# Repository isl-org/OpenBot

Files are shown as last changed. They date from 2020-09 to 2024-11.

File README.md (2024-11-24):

<a href="https://www.openbot.org/" target="_blank">
  Banner
</a>

<h1 align="center"><a>Turning Smartphones into Robots</a></h1>

<p align="center">
   </a>
   </a>
   </a>
   </a>
   </a>
   </a>
   </a>
   </a>
</p>

<p align="center">
  <span>English</span> |
  <a href="README.zh-CN.md">简体中文</a> |
  <a href="README.de-DE.md">Deutsch</a> |
  <a href="README.fr-FR.md">Français</a> |
  <a href="README.es-ES.md">Español</a> |
  <a href="README.ko-KR.md">한국어</a>
</p>

OpenBot leverages smartphones as brains for low-cost robots. We have designed a small electric vehicle that costs about $50 and serves as a robot body. Our software stack for Android smartphones supports advanced robotics workloads such as person following and real-time autonomous navigation.

## Get started with OpenBot

- Read the [Disclaimer](DISCLAIMER.md)
- Build your own [Robot Body](body/README.md)
- Flash the [Arduino Firmware](firmware/README.md)
- Install the [Android Apps](android/README.md)
- Drive the robot via a [Controller](controller/README.md)
- Program your robot in the [Playground](open-code/README.md)
- Train your own [Driving Policy](policy/README.md)

## Get the source code

- You can download the repo as a [zip file](https://github.com/intel-isl/OpenBot/archive/master.zip) and extract it into a folder of your choice.
- You can clone the OpenBot repository from GitHub with the following command:
    ```bash
    git clone https://github.com/intel-isl/OpenBot.git
    ```
- You can fork the OpenBot repository and then clone your local copy. This is recommended, especially if you want to [contribute](CONTRIBUTING.md).

## Videos

<a href="https://www.youtube.com/watch?v=RbzPXywJifA" >
  youtube video
</a>

<a href="https://www.youtube.com/watch?v=qc8hFLyWDOM" >
  youtube video
</a>

## Cool projects using OpenBot

There are a lot of cool projects using OpenBot already. Below is a small selection. Click on the images to be redirected to the respective projects.

<p float="left">
  <a href="https://www.thingiverse.com/thing:4670884" target="_blank">
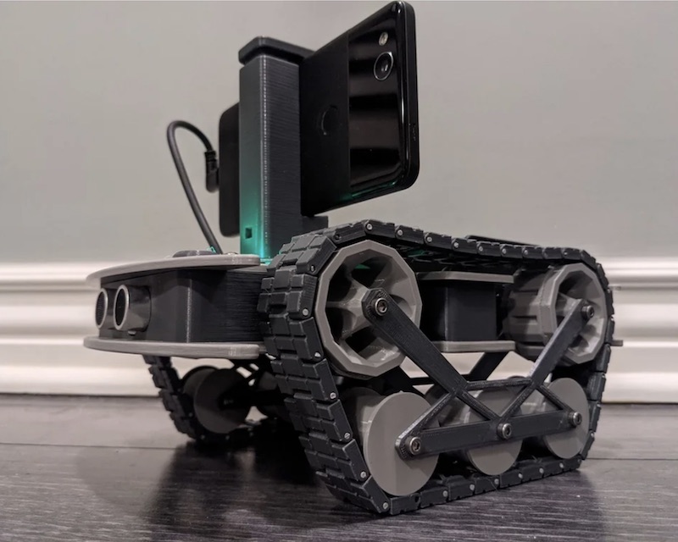
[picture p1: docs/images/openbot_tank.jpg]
Tank OpenBot
    
  </a>
  <a href="https://diyrobocars.com/2020/12/14/an-improved-version-of-the-intel-openbot" target="_blank">
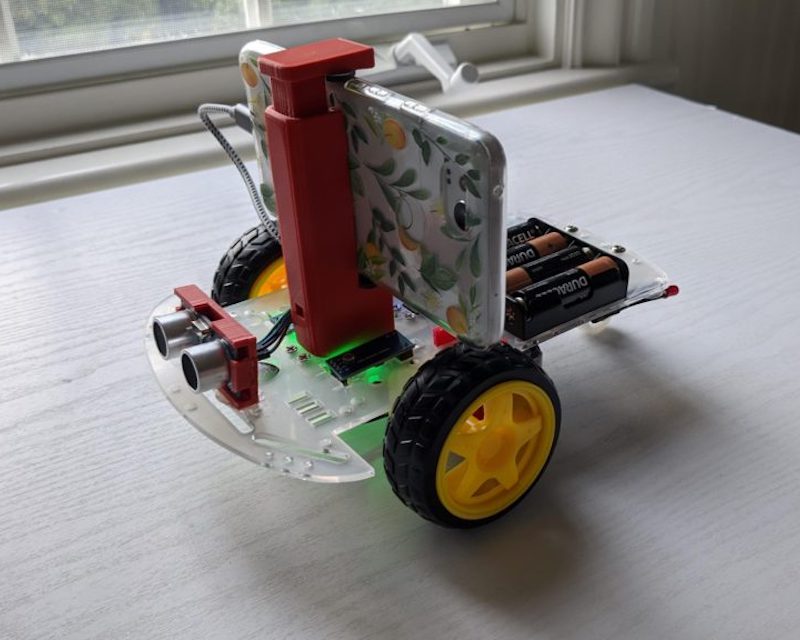
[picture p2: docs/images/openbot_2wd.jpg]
2WD OpenBot
    
  </a>
  <a href="https://custom-build-robots.com/raspberry-pi-robot-cars/openbot-your-smartphone-controls-a-robot-car-introduction/13860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" target="_blank">
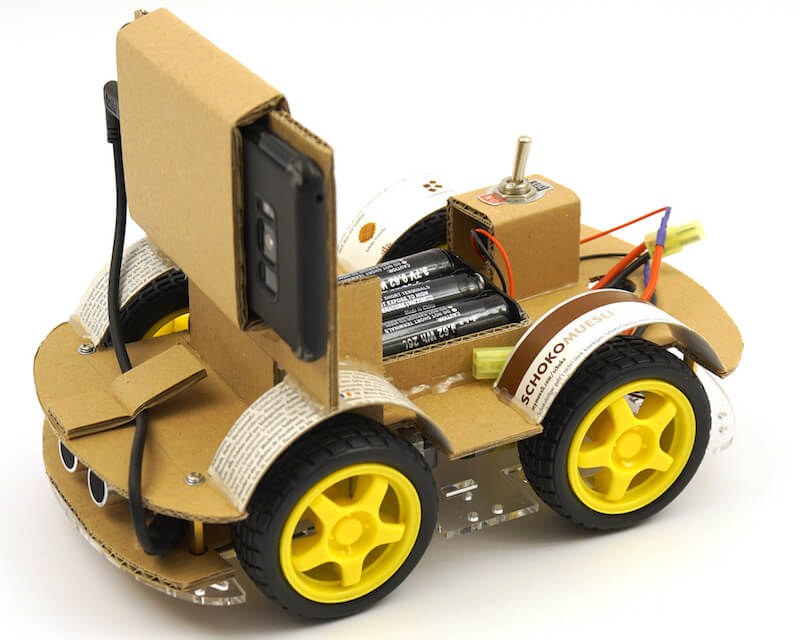
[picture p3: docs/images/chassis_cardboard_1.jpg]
Cardboard OpenBot
    
  </a>
  <a href="https://www.youtube.com/watch?v=PEj8jWapGt4" target="_blank">
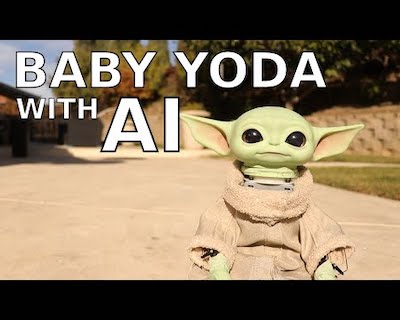
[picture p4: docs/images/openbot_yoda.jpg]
Baby Yoda OpenBot
    
  </a>
</p>

## Contact

- Join our [Slack](https://join.slack.com/t/openbot-community/shared_invite/zt-jl8ygxqt-WNRNi9yzh7Lu60qui6Nh6w) channel to connect with the OpenBot community.
- Contact us via [Email](mailto:openbot.team@gmail.com)

## Contribute

Please read the [contribution guidelines](CONTRIBUTING.md). If you are not sure where to start have a look at the [open issues](https://github.com/intel-isl/OpenBot/issues).

## Citation

Please cite our [paper](https://arxiv.org/abs/2008.10631) if you use OpenBot.

```bib
@inproceedings{mueller2021openbot,
    title     = {OpenBot: Turning Smartphones into Robots},
    author    = {M{\"u}ller, Matthias and Koltun, Vladlen},
    booktitle = {Proceedings of the International Conference on Robotics and Automation (ICRA)},
    year = {2021},
}
```

<a href="https://www.openbot.org//" target="_blank">
  Footer
</a>

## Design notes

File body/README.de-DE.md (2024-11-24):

# OpenBot: Roboterkörper

<p align="center">
  <a href="README.md">English</a> |
  <a href="README.zh-CN.md">简体中文</a> |
  <span>Deutsch</span> |
  <a href="README.fr-FR.md">Français</a> |
  <a href="README.es-ES.md">Español</a> |
  <a href="README.ko-KR.md">한국어</a>
</p>

Sie können einen [Ready-to-Run (RTR)](rtr) OpenBot auf Amazon kaufen:
- [RTR-TT](https://buy.openbot.org/rtr-tt)
- [RTR-520](https://buy.openbot.org/rtr-520)

Für größere Bestellungen kontaktieren Sie uns bitte per E-Mail.

## Eigenbau

Sie können einen beliebigen Roboterkörper mit Rädern um einen Mikrocontroller wie den Arduino Nano herum bauen, um ihn mit der OpenBot-Software zu verwenden. Wir haben einen [3D-gedruckten Körper](diy) für einen Roboter mit Rädern entworfen, der auf kostengünstiger, leicht verfügbarer Hobby-Hardware basiert. [OpenBot Lite](lite) ist eine kleinere und vereinfachte Variante der OpenBot DIY-Version, die für Bildungszwecke entwickelt wurde. Selbst wenn Sie ihn nicht bauen möchten, könnten Sie die [Schritt-für-Schritt-Videoanleitungen](lite/#step-by-step-video-guides) hilfreich finden. Wir haben auch einen [3D-gedruckten Körper](rc_truck) für kommerziell erhältliche 1:16 RC-Trucks (wie [diesen](https://www.amazon.de/dp/B00M3J7DJW)) entworfen. Zudem bieten wir Baupläne für ein [Multi-Terrain-Fahrzeug](mtv) an, das als Allzweckplattform für Outdoor-Projekte mit dem OpenBot-Framework dient.

Im Folgenden finden Sie einige Beispiele mit Bauanleitungen und weiteren Details:

<table style="width:100%;border:none;text-align:center">
  <tr>
  <td>  <a href="diy">
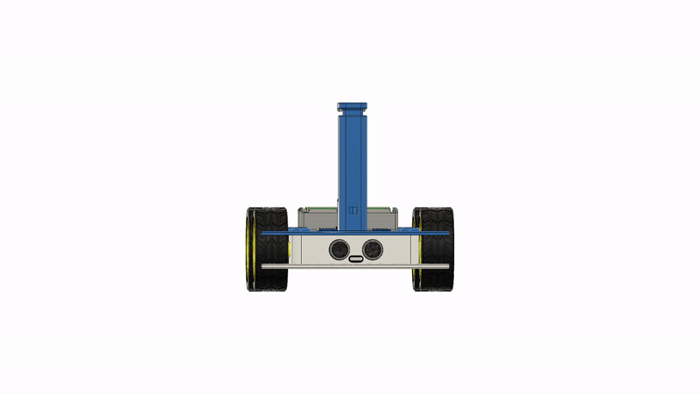
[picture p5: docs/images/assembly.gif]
DIY
    
  </a>
  </td>
  <td>
  <a href="lite">
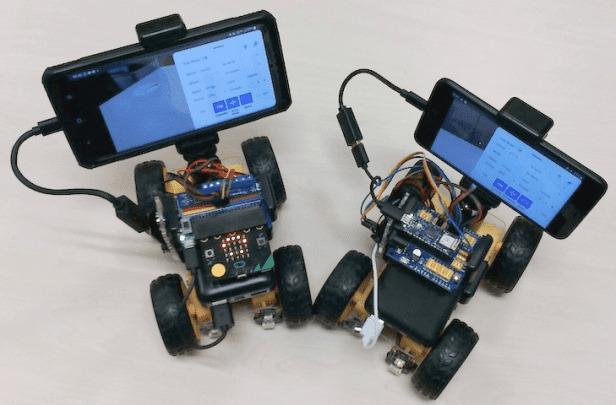
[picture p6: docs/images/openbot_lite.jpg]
Lite
    
  </a>
  </td>
  <td>
  <a href="rc_truck">
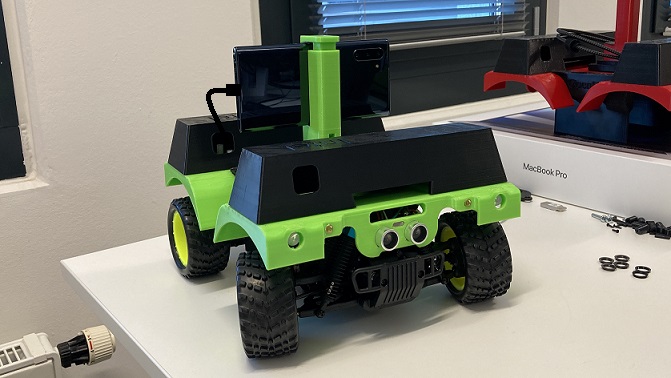
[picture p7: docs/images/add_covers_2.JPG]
RC Truck
    
  </a>
  </td>
  <td>
  <a href="mtv">
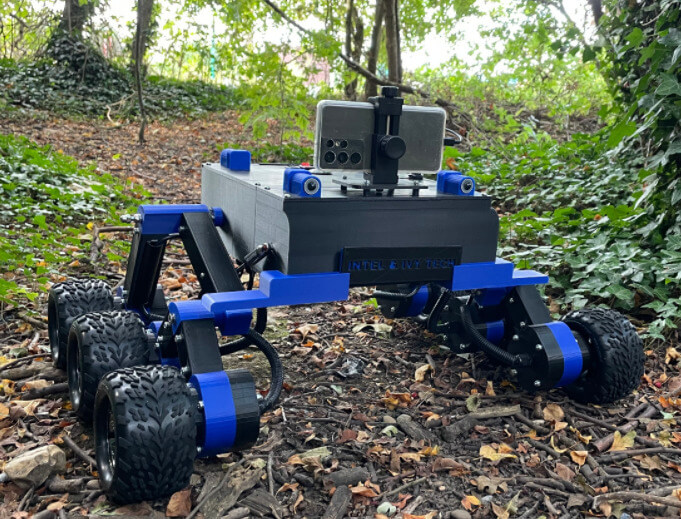
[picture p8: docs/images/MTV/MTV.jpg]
Multi-Terrain Vehicle
    
  </a>
  </td>
  <td>
  <a href="rtr">
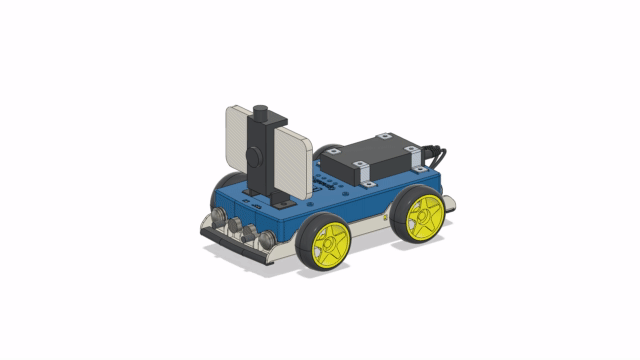
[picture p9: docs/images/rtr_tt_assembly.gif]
RTR
    
  </a>
  </td>
  </tr>
  <tr>
    <td><a href="diy"> DIY </a></td>
    <td><a href="lite"> Lite </a></td>
    <td><a href="rc_truck"> RC Truck </a></td>
    <td><a href="mtv"> Multi-Terrain Vehicle </a></td>
    <td><a href="rtr"> RTR </a></td>
  </tr>
</table>

## Weiter

Flashen Sie die [Arduino-Firmware](../firmware/README.md)

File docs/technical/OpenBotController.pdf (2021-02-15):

# OpenBot Controller technical Overview

Ivo Zivkov
izivkov@gmail.com
Date: January 2nd, 2021

## Introduction

The OpenBot controller (controller) is an Android Application for remotely controlling the OpenBot (https://www.openbot.org/) vehicle (robot). It communicates with the main OpenBot android application running on the robot’s phone. Here is an image of the main screen:

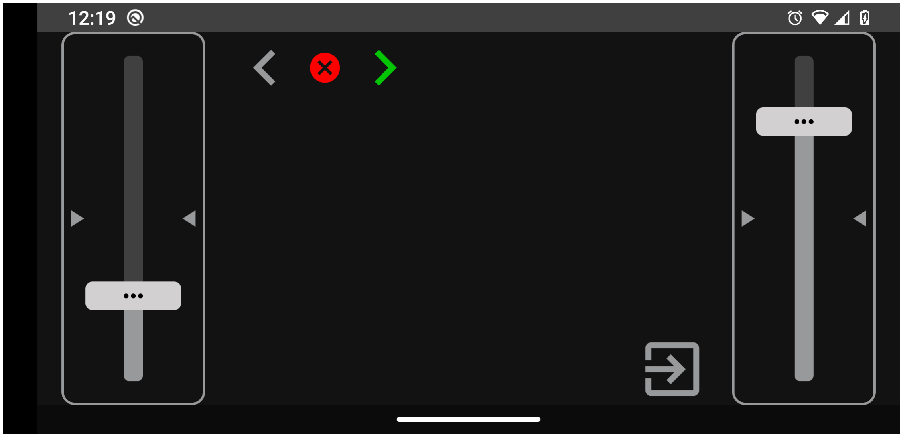
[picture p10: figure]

## Connecting to the OpenBot

The controller establishes connection to the robot via the Android Nearby Connections (https://developers.google.com/nearby/connections/overview) API. This technology uses Bluetooth or WiFi to quickly connect to another device. The connection type may change in the future, as we may require WiFi-only connection in order to send video stream from the robot to the controller.

Upon starting, the controller advertises its presence using the Nearby API’s. When the “Phone” control is selected on the robot’s menu, the robot starts a “Discovery” process, looking for advertisers. This process will be automatically terminated after one minute to save batteries, in case no connection is made.

There is also another type of connection, WiFiDirectConnection, which is based on WiFi direct API (https://developer.android.com/training/connect-devices-wirelessly/wifi-direct) from Google. It is not currently in use by the controller, but other devices, like Raspberry PI, can take advantage of this connection. Both NearbyConnection and WiFiDirectConnection implement

ILocalConnection interface, so they are easily swapped. The controller app also has both connections implemented, so the connection types in the Main Bot app should match the type in the Controller.

## Data Flow

After connection, the robot and the controller establish a two-way communication:

1. The controller sends commands to the robot
2. The robot sends status information to the controller.

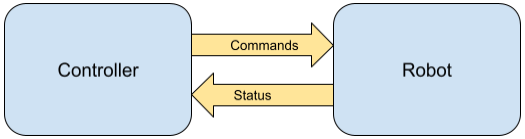
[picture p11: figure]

## Data Format

Both commands and status information are in JSON format. Currently, the following commands are supported:

### 1. Commands:

{command: “LOGS”} - toggle Logging

{command: “NOISE”} - toggle Noise

{command: “INDICATOR_LEFT”} - turn on left indicator, turn off right indicator if ON

{command: “INDICATOR_RIGHT”} - turn on right indicator, turn off left indicator if ON

{command: “INDICATOR_STOP”} - turn off right and left indicators

{command: “NETWORK”} - toggle network

{command: “DRIVE_MODE”} - cycle between drive modes: DUAL, GAME, JOYSTICK

{driveCmd: {l:0.2, r:-0.34}} - Send a drive command to the robot. The “l” and “r” values indicate the speed of left and right wheels, and can only be between -1 and 1.. Negative numbers indicate reverse. This is how the robot is steered.

### 2. Status

Status data is sent from the robot to controller to indicate the current state of the robot. The controller can display its components according to this information. The status can be sent at any time. The robot application observes for changes in its state, and sends status data to the controller upon changes. Status data can be sent one value at a time, or in bulk.

{status: {“LOGS”: “true | false”}}
{status: {“NOISE”: “true | false”}}
{status: {“NETWORK”: “true | false”}}
{status: {“DRIVE_MODE”: “game | dual | joystick”}}

{status: {“INDICATE_LEFT”: “true|false”}}

{status: {“INDICATE_RIGHT”: “true|false”}}

{status: {“INDICATE_STOP”: “true|false”}}

Or bulk mode:

{status: {“INDICATE_STOP”: “false”, “NOISE”: “true”, “DRIVE_MODE”: “dual”}}

## How Commands and Status is Handled in the Robot

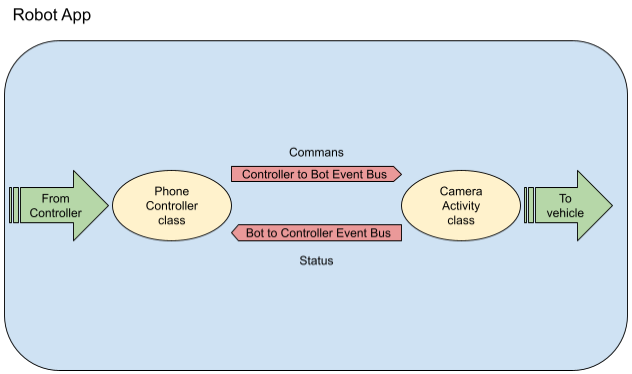
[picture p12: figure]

The robot app provides two channels of communication between the main CameraActivity class and the PhoneController class.

The PhoneController class handles the interface to the Controller connection. In this case, it uses the NearbyConnection class to receive and send data to the remote controller. Once data is received, the PhoneController class sends an RX event (http://reactivex.io/RxJava/javadoc/io/reactivex/subjects/PublishSubject.html) to the CameraActivity via the ControllerToBotEventBus. The ControllerToBotEventBus class handles all the details, so to send command event is really simple:

ControllerToBotEventBus.emitEvent(new JSONObject({command: ”LOGS”}));

To receive a status events from the CameraActivity class is also simple. Subscribe to status events like this:

BotToControllerEventBus.getProcessor().subscribe(event -> handleThisEvent(event));

In our case, we simply send back the status information to the controller using the NearbyConnection class:

BotToControllerEventBus.getProcessor().subscribe(event -> send(event));

… where the send(event) functions send the data to the controller.

Note that using event buses makes it easy for other remote devices to issue commands to the robot, without the need to change any code in the CameraActivity and NetworkActivity classes. For example, if we are adding a web client for controlling the robot, we can create a class similar to the PhoneController to receive commands from the web server in any format, then just create and emit an event and send it via the ControllerToBotEventBus. The rest of the app can be treated as a black box.

## Controller Internals

The controller app is written in Kotlin. Most of the app’s logic is handled by custom components (buttons, sliders) which send their own commands, and receive status information related to them from the robot. The custom components may change their appearance depending on the status they have received from the robot. For example, if the robot reports that the Noise function has been turned on, the Noise button will change its color to reflect that state. Drive control commands are sent from the Right and Left DualDriveSeekBar components, which appear as sliders on each side of the controller screen.

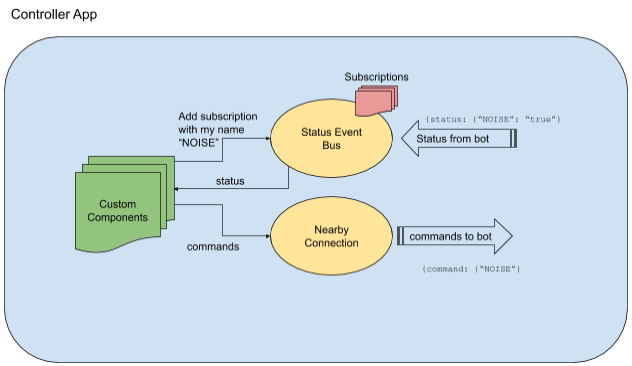
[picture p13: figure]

Components listen on “TouchEvents” from the user and send commands to the controller. Each component will send a different command. For example a Noise button will send command:

{command: “NOISE”}

Each component has a name associated with it. To get back status events, the component will subscribe with StatusEventBus class to receive events on this subject (name). In the example above, the status message would be:

{status: {“NOISE”, “true”}}

The BotDataListen class (not shown) will match the event name “NOISE” with the name of the subject “NOISE” and will instruct StatusEventBus to send the event on this subject. The component which subscribed to the “NOISE” subject will receive the value, and will update its appearance.

## Putting it all together

Let us trace all the steps that take place when the user presses the “INDICATOR_RIGHT” button on the controller (this is the blinking green arrow on the top-left of the first diagram in this document).

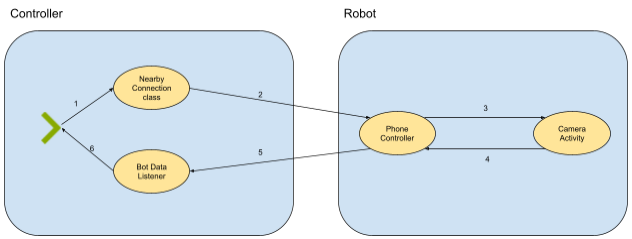
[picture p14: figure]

1. The user presses the green arrow button. This generates TouchEvent, and invokes the send() method on the NearbyConnection class to send {command: “INDICATOR_RIGHT”} command to the controller.
2. The NearbyConnection class sends the command to the controller.
3. PhoneController class in the robot app detects a new command has arrived, and passes it on to the CameraActivity
4. The event is received by the CameraActivity class, and the command is passed to the Vehicle class (not shown) to turn on the signal in the robot.
This state change is detected and the CameraActivity sends a status command:

{status: {“INDICATOR_RIGH”, “true”}}

to the PhoneController.

5. The PhoneController routes the status back to the controller, and there it is received by BotDataListener class.
6. BotDataListener routes the status message to the correct custom control via the StatusEventBus class and using INDICATOR_RIGH as the subject. The component receives the status messages and starts animation to blink every second. It will stop the animation if it receives {status: {“INDICATOR_RIGH”, “false”}} message.

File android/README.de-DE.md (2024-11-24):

# Android Apps

<p align="center">
  <a href="README.md">English</a> |
  <a href="README.zh-CN.md">简体中文</a> |
  <span>Deutsch</span> |
  <a href="README.fr-FR.md">Français</a> |
  <a href="README.es-ES.md">Español</a> |
  <a href="README.ko-KR.md">한국어</a>
</p>

## Funktionen

Klicken Sie auf die untenstehenden Links, um mehr über die Funktionen der Apps zu erfahren.

- [Robot App](robot/README.md)
- [Controller App](controller/README.md)

## Installation der Apps

Der einfachste Weg, eine der Apps zu erhalten, ist, sie direkt auf das Telefon herunterzuladen, indem Sie den entsprechenden QR-Code verwenden. Wenn Sie den Browser auf Ihrem Telefon verwenden, können Sie auch einfach auf den QR-Code klicken. Sie können dann die APK auf Ihrem Telefon öffnen und [installieren](https://www.lifewire.com/install-apk-on-android-4177185). Beachten Sie, dass die APK nur mit einem Debug-Schlüssel signiert ist.

<table style="width:100%;border:none;text-align:center">
  <tr>
    <td>  <a href="https://app.openbot.org/robot" target="_blank">
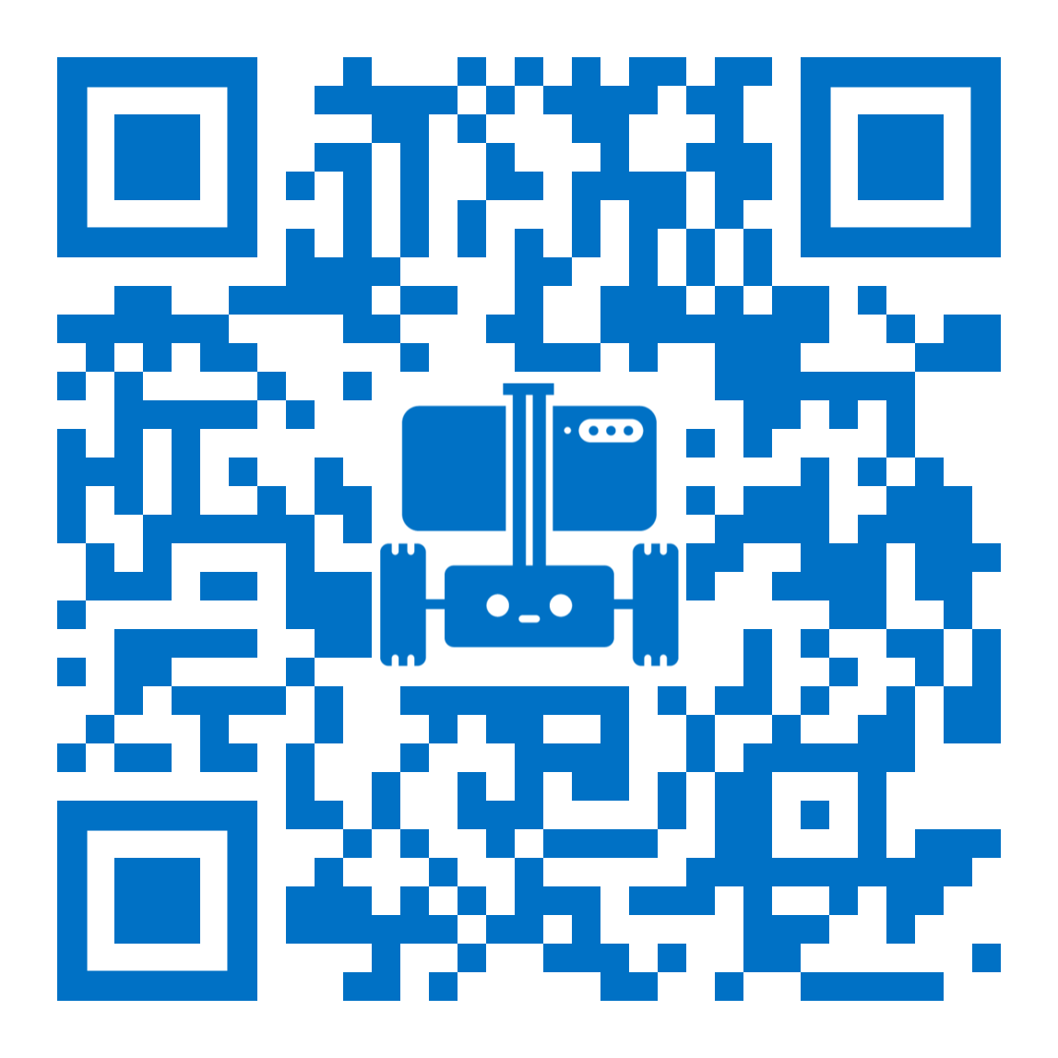
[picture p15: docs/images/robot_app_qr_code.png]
🤖 App
    
  </a>
    </td>
    <td>
  <a href="https://app.openbot.org/controller" target="_blank">
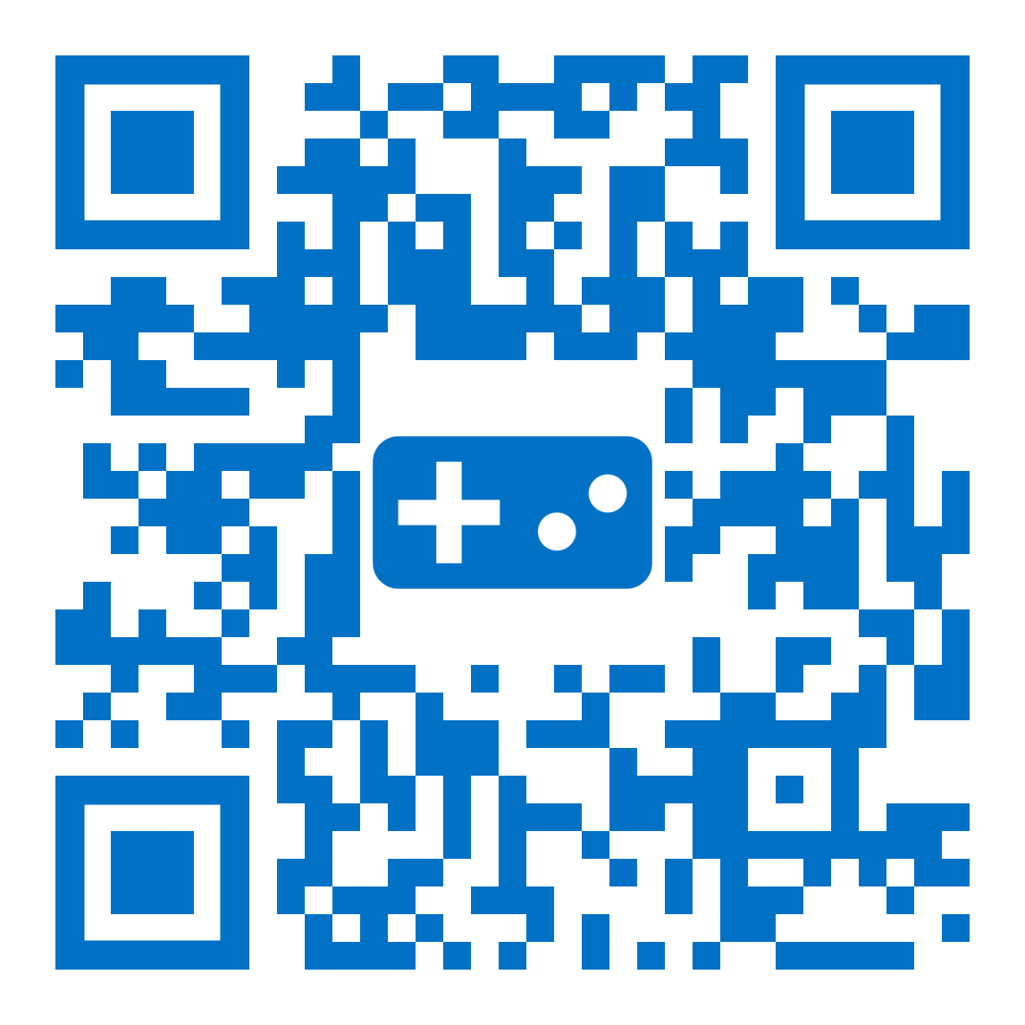
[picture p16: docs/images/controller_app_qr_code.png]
🎮 App
    
  </a>
      </td>
  </tr>
  <tr>
    <td>🤖 App</td>
    <td>🎮 App</td>
  </tr>
</table>

Alternativ können Sie die APKs aus den Assets einer beliebigen [Veröffentlichung](https://github.com/intel-isl/OpenBot/releases) herunterladen. Wenn Sie die neueste App aus dem Master-Branch möchten, können Sie sie auch aus den Build-Artefakten [hier](https://github.com/intel-isl/OpenBot/actions?query=workflow%3A%22Java+CI+with+Gradle%22) herunterladen. Beachten Sie, dass sie möglicherweise nicht stabil ist. Wenn Sie später Änderungen an der App vornehmen möchten, folgen Sie den untenstehenden Schritten, um die App zu kompilieren und auf Ihrem Telefon zu installieren.

## Apps bauen

### Voraussetzungen

- [Android Studio Electric Eel | 2022.1.1 oder später](https://developer.android.com/studio/index.html) zum Bauen und Installieren der APKs.
- Android-Gerät und Android-Entwicklungsumgebung mit mindestens API 21.
- Derzeit verwenden wir API 33 als Compile-SDK und API 32 als Target-SDK. Es sollte automatisch installiert werden, aber falls nicht, können Sie das SDK manuell installieren. Gehen Sie zu Android Studio -> Einstellungen -> Erscheinungsbild & Verhalten -> Systemeinstellungen -> Android SDK. Stellen Sie sicher, dass API 33 aktiviert ist, und klicken Sie auf Anwenden.

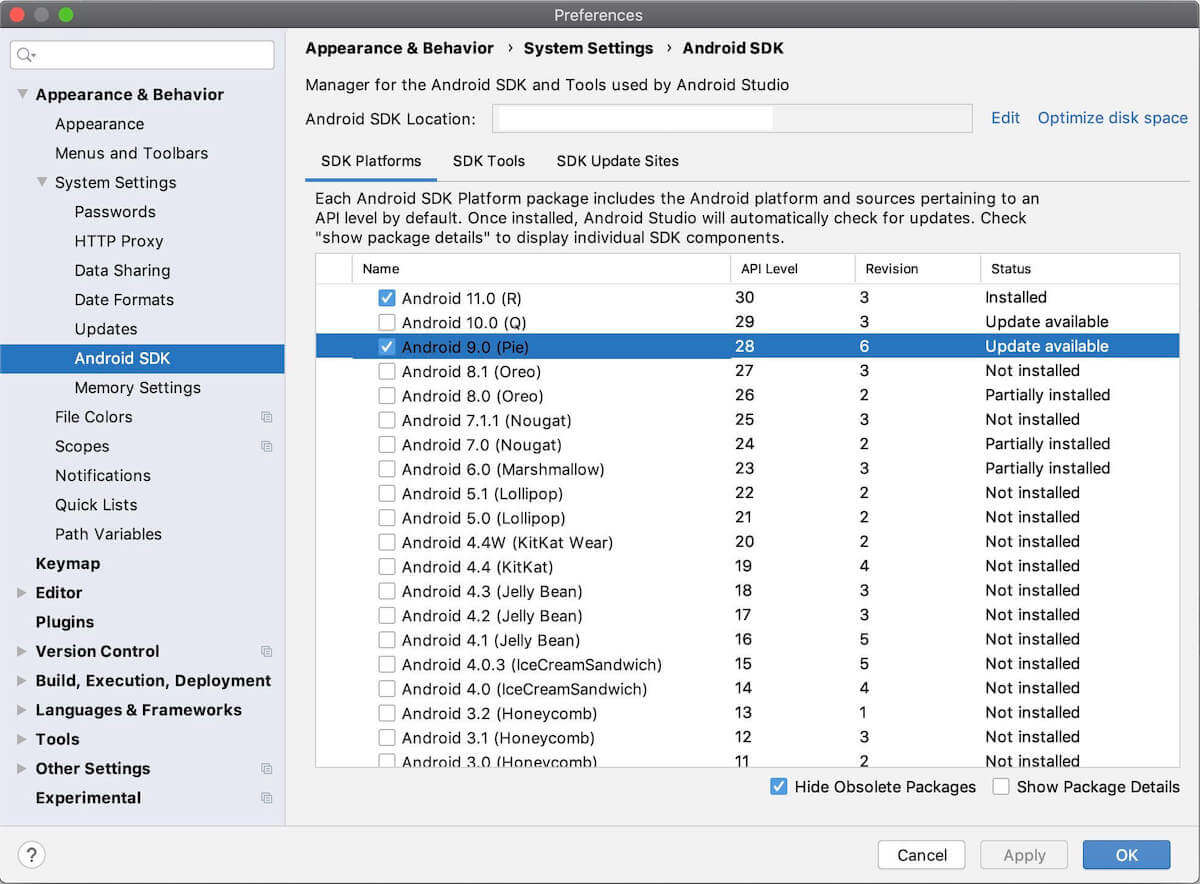
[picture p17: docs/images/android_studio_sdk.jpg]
Android SDK


### Build-Prozess

1. Öffnen Sie Android Studio und wählen Sie *Ein bestehendes Android Studio-Projekt öffnen*.
2. Wählen Sie das Verzeichnis OpenBot/android und klicken Sie auf OK.
3. Wenn Sie die [OpenBot-App](app/README.md) installieren möchten, stellen Sie sicher, dass die *app*-Konfiguration ausgewählt ist. Wenn Sie die [Controller-App](controller/README.md) installieren möchten, wählen Sie die *controller*-Konfiguration. Bestätigen Sie den Gradle-Sync, falls erforderlich. Um einen Gradle-Sync manuell durchzuführen, klicken Sie auf das Gradle-Symbol.
  Gradle Sync
4. Verbinden Sie Ihr Android-Gerät und stellen Sie sicher, dass USB-Debugging in den [Entwickleroptionen](https://developer.android.com/studio/debug/dev-options) aktiviert ist. Abhängig von Ihrer Entwicklungsumgebung könnten [weitere Schritte](https://developer.android.com/studio/run/device) erforderlich sein. Sie sollten Ihr Gerät jetzt in der Navigationsleiste oben sehen.
  Phone
5. Klicken Sie auf die Schaltfläche Ausführen (der grüne Pfeil) oder wählen Sie Ausführen > 'android' ausführen aus dem oberen Menü. Möglicherweise müssen Sie das Projekt mit Build > Projekt neu erstellen neu erstellen.
  Run
6. Wenn Sie gefragt werden, ob Sie Instant Run verwenden möchten, klicken Sie auf *Ohne Instant Run fortfahren*.

### Fehlerbehebung

#### Versionen

Wenn Sie eine Nachricht wie `Das Projekt verwendet eine inkompatible Version (AGP 7.4.0) des Android Gradle-Plugins. Die neueste unterstützte Version ist AGP 7.3.0` erhalten, müssen Sie Android Studio aktualisieren oder Ihr Gradle-Plugin downgraden. Sie können mehr über die Versionskompatibilität zwischen Android Studio und dem Gradle-Plugin [hier](https://developer.android.com/studio/releases/gradle-plugin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) lesen.

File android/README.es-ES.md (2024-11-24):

# Aplicaciones Android

<p align="center">
  <a href="README.md">English</a> |
  <a href="README.zh-CN.md">简体中文</a> |
  <a href="README.de-DE.md">Deutsch</a> |
  <a href="README.fr-FR.md">Français</a> |
  <span>Español</span> |
  <a href="README.ko-KR.md">한국어</a>
</p>

## Características

Haz clic en los enlaces a continuación para leer sobre las características de las aplicaciones.

- [Aplicación Robot](robot/README.es-ES.md)
- [Aplicación Controlador](controller/README.es-ES.md)

## Instalar las aplicaciones

La forma más fácil de obtener cualquiera de las aplicaciones es descargándola directamente al teléfono usando el código QR correspondiente. Si estás en el navegador del teléfono, también puedes hacer clic en el código QR. Luego puedes abrir el apk en tu teléfono e [instalarlo](https://www.lifewire.com/install-apk-on-android-4177185). Ten en cuenta que el apk solo está firmado con una clave de depuración.

<table style="width:100%;border:none;text-align:center">
  <tr>
    <td>  <a href="https://app.openbot.org/robot" target="_blank">
    🤖 App
  </a>
    </td>
    <td>
  <a href="https://app.openbot.org/controller" target="_blank">
    🎮 App
  </a>
      </td>
  </tr>
  <tr>
    <td>🤖 App</td>
    <td>🎮 App</td>
  </tr>
</table>

Alternativamente, puedes descargar los apks desde los assets de cualquier [release](https://github.com/intel-isl/OpenBot/releases). Si deseas la última aplicación de la rama principal, también puedes descargarla desde los artefactos de compilación [aquí](https://github.com/intel-isl/OpenBot/actions?query=workflow%3A%22Java+CI+with+Gradle%22). Ten en cuenta que puede no ser estable. Si deseas realizar cambios en la aplicación más adelante, sigue los pasos a continuación para compilar la aplicación y desplegarla en tu teléfono.

## Compilar las aplicaciones

### Requisitos previos

- [Android Studio Electric Eel | 2022.1.1 o posterior](https://developer.android.com/studio/index.html) para compilar e instalar los apks.
- Dispositivo Android y entorno de desarrollo Android con API mínima 21.
- Actualmente, usamos API 33 como SDK de compilación y API 32 como SDK de destino. Debería instalarse automáticamente, pero si no es así, puedes instalar el SDK manualmente. Ve a Android Studio -> Preferences -> Appearance & Behaviour -> System Settings -> Android SDK. Asegúrate de que API 33 esté marcada y haz clic en aplicar.

Android SDK

### Proceso de compilación

1. Abre Android Studio y selecciona *Open an existing Android Studio project*.
2. Selecciona el directorio OpenBot/android y haz clic en OK.
3. Si deseas instalar la [aplicación OpenBot](app/README.es-ES.md) asegúrate de seleccionar la configuración *app*. Si deseas instalar la [aplicación Controlador](controller/README.es-ES.md), selecciona la configuración *controller*. Confirma la sincronización de Gradle si es necesario. Para realizar una sincronización de Gradle manualmente, haz clic en el icono de gradle.
  Gradle Sync
4. Conecta tu dispositivo Android y asegúrate de que la depuración USB en las [opciones de desarrollador](https://developer.android.com/studio/debug/dev-options) esté habilitada. Dependiendo de tu entorno de desarrollo, pueden ser necesarios [otros pasos](https://developer.android.com/studio/run/device). Ahora deberías ver tu dispositivo en la barra de navegación superior.
  Phone
5. Haz clic en el botón de ejecutar (la flecha verde) o selecciona Run > Run 'android' desde el menú superior. Es posible que necesites reconstruir el proyecto usando Build > Rebuild Project.
  Run
6. Si te pregunta si deseas usar Instant Run, haz clic en *Proceed Without Instant Run*.

### Solución de problemas

#### Versiones

Si recibes un mensaje como `The project is using an incompatible version (AGP 7.4.0) of the Android Gradle plugin. Latest supported version is AGP 7.3.0` necesitas actualizar Android Studio o degradar tu plugin de gradle. Puedes leer más sobre la compatibilidad de versiones entre Android Studio y el plugin de gradle [aquí](https://developer.android.com/studio/releases/gradle-plugin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).

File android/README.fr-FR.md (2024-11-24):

# Applications Android

<p align="center">
  <a href="README.md">English</a> |
  <a href="README.zh-CN.md">简体中文</a> |
  <a href="README.de-DE.md">Deutsch</a> |
  <span>Français</span> |
  <a href="README.es-ES.md">Español</a> |
  <a href="README.ko-KR.md">한국어</a>
</p>

## Fonctionnalités

Cliquez sur les liens ci-dessous pour en savoir plus sur les fonctionnalités des applications.

- [Application Robot](robot/README.md)
- [Application Contrôleur](controller/README.md)

## Installer les applications

Le moyen le plus simple d'obtenir l'une des applications est de la télécharger directement sur le téléphone en utilisant le code QR correspondant. Si vous êtes sur le navigateur du téléphone, vous pouvez également cliquer sur le code QR. Vous pouvez ensuite ouvrir le fichier apk sur votre téléphone et [l'installer](https://www.lifewire.com/install-apk-on-android-4177185). Notez que l'apk est uniquement signé avec une clé de débogage.

<table style="width:100%;border:none;text-align:center">
  <tr>
    <td>  <a href="https://app.openbot.org/robot" target="_blank">
    🤖 App
  </a>
    </td>
    <td>
  <a href="https://app.openbot.org/controller" target="_blank">
    🎮 App
  </a>
      </td>
  </tr>
  <tr>
    <td>🤖 App</td>
    <td>🎮 App</td>
  </tr>
</table>

Alternativement, vous pouvez télécharger les fichiers apk depuis les assets de n'importe quelle [release](https://github.com/intel-isl/OpenBot/releases). Si vous souhaitez obtenir la dernière version de l'application à partir de la branche master, vous pouvez également la télécharger depuis les artefacts de build [ici](https://github.com/intel-isl/OpenBot/actions?query=workflow%3A%22Java+CI+with+Gradle%22). Notez qu'elle peut ne pas être stable. Si vous souhaitez apporter des modifications à l'application plus tard, suivez les étapes ci-dessous pour compiler l'application et la déployer sur votre téléphone.

## Compiler les applications

### Prérequis

- [Android Studio Electric Eel | 2022.1.1 ou plus récent](https://developer.android.com/studio/index.html) pour compiler et installer les fichiers apk.
- Un appareil Android et un environnement de développement Android avec un API minimum de 21.
- Actuellement, nous utilisons l'API 33 comme SDK de compilation et l'API 32 comme SDK cible. Il devrait s'installer automatiquement, mais si ce n'est pas le cas, vous pouvez installer le SDK manuellement. Allez dans Android Studio -> Préférences -> Apparence et comportement -> Paramètres système -> SDK Android. Assurez-vous que l'API 33 est cochée et cliquez sur appliquer.

SDK Android

### Processus de compilation

1. Ouvrez Android Studio et sélectionnez *Ouvrir un projet Android Studio existant*.
2. Sélectionnez le répertoire OpenBot/android et cliquez sur OK.
3. Si vous souhaitez installer l'[application OpenBot](app/README.md), assurez-vous de sélectionner la configuration *app*. Si vous souhaitez installer l'[application Contrôleur](controller/README.md), sélectionnez la configuration *controller*. Confirmez la synchronisation Gradle si nécessaire. Pour effectuer une synchronisation Gradle manuellement, cliquez sur l'icône Gradle.
  Synchronisation Gradle
4. Connectez votre appareil Android et assurez-vous que le débogage USB dans les [options développeur](https://developer.android.com/studio/debug/dev-options) est activé. Selon votre environnement de développement, [d'autres étapes](https://developer.android.com/studio/run/device) peuvent être nécessaires. Vous devriez maintenant voir votre appareil dans la barre de navigation en haut.
  Téléphone
5. Cliquez sur le bouton Exécuter (la flèche verte) ou sélectionnez Exécuter > Exécuter 'android' dans le menu supérieur. Vous devrez peut-être reconstruire le projet en utilisant Build > Rebuild Project.
  Exécuter
6. Si on vous demande d'utiliser Instant Run, cliquez sur *Continuer sans Instant Run*.

### Dépannage

#### Versions

Si vous recevez un message tel que `Le projet utilise une version incompatible (AGP 7.4.0) du plugin Gradle Android. La dernière version prise en charge est AGP 7.3.0`, vous devez mettre à jour Android Studio ou rétrograder votre plugin Gradle. Vous pouvez en savoir plus sur la compatibilité des versions entre Android Studio et le plugin Gradle [ici](https://developer.android.com/studio/releases/gradle-plugin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).

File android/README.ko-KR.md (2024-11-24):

# 안드로이드 앱

<p align="center">
  <a href="README.md">English</a> |
  <a href="README.zh-CN.md">简体中文</a> |
  <a href="README.de-DE.md">Deutsch</a> |
  <a href="README.fr-FR.md">Français</a> |
  <a href="README.es-ES.md">Español</a> |
  <span>한국어</span>
</p>

## 기능

아래 링크를 클릭하여 앱의 기능에 대해 읽어보세요.

- [로봇 앱](robot/README.md)
- [컨트롤러 앱](controller/README.md)

## 앱 설치하기

앱을 얻는 가장 쉬운 방법은 해당 QR 코드를 사용하여 직접 전화로 다운로드하는 것입니다. 전화 브라우저에서 QR 코드를 클릭하면 됩니다. 그런 다음 휴대폰에서 apk를 열고 [설치](https://www.lifewire.com/install-apk-on-android-4177185)할 수 있습니다. 참고로 apk는 디버그 키로만 서명되어 있습니다.

<table style="width:100%;border:none;text-align:center">
  <tr>
    <td>  <a href="https://app.openbot.org/robot" target="_blank">
    🤖 앱
  </a>
    </td>
    <td>
  <a href="https://app.openbot.org/controller" target="_blank">
    🎮 앱
  </a>
      </td>
  </tr>
  <tr>
    <td>🤖 앱</td>
    <td>🎮 앱</td>
  </tr>
</table>

대안으로, [릴리스](https://github.com/intel-isl/OpenBot/releases)의 자산에서 apk를 다운로드할 수 있습니다. 최신 앱을 마스터 브랜치에서 원하신다면, [여기](https://github.com/intel-isl/OpenBot/actions?query=workflow%3A%22Java+CI+with+Gradle%22)에서 빌드 아티팩트로 다운로드할 수 있습니다. 안정적이지 않을 수 있습니다. 앱을 나중에 변경하고 싶다면 아래 단계를 따라 앱을 컴파일하고 휴대폰에 배포하세요.

## 앱 빌드하기

### 필수 조건

- [Android Studio Electric Eel | 2022.1.1 이상](https://developer.android.com/studio/index.html)으로 apk를 빌드하고 설치합니다.
- 최소 API 21을 갖춘 Android 기기 및 Android 개발 환경이 필요합니다.
- 현재 API 33을 컴파일 SDK로, API 32를 타겟 SDK로 사용합니다. 자동으로 설치되어야 하지만, 그렇지 않은 경우 수동으로 SDK를 설치할 수 있습니다. Android Studio -> Preferences -> Appearance & Behaviour -> System Settings -> Android SDK로 이동합니다. API 33이 체크되어 있는지 확인하고 적용을 클릭하세요.

Android SDK

### 빌드 과정

1. Android Studio를 열고 *기존 Android Studio 프로젝트 열기*를 선택합니다.
2. OpenBot/android 디렉토리를 선택하고 OK를 클릭합니다.
3. [OpenBot 앱](app/README.md)을 설치하려면 *app* 구성을 선택합니다. [컨트롤러 앱](controller/README.md)을 설치하려면 *controller* 구성을 선택합니다. 필요한 경우 Gradle Sync를 확인합니다. 수동으로 Gradle Sync를 수행하려면 gradle 아이콘을 클릭하세요.
   Gradle Sync
4. Android 기기를 연결하고 [개발자 옵션](https://developer.android.com/studio/debug/dev-options)에서 USB 디버깅이 활성화되어 있는지 확인합니다. 개발 환경에 따라 [추가 단계](https://developer.android.com/studio/run/device)가 필요할 수 있습니다. 이제 상단 내비게이션 바에서 기기를 확인할 수 있어야 합니다.
   전화
5. 실행 버튼(초록색 화살표)을 클릭하거나 상단 메뉴에서 Run > Run 'android'를 선택합니다. Build > Rebuild Project를 사용하여 프로젝트를 다시 빌드해야 할 수도 있습니다.
   실행
6. Instant Run을 사용하라는 메시지가 나타나면 *Proceed Without Instant Run*을 클릭하세요.

### 문제 해결

#### 버전

`The project is using an incompatible version (AGP 7.4.0) of the Android Gradle plugin. Latest supported version is AGP 7.3.0`와 같은 메시지가 나타나면 Android Studio를 업그레이드하거나 gradle 플러그인을 다운그레이드해야 합니다. Android Studio와 gradle 플러그인 간의 버전 호환성에 대한 자세한 내용은 [여기](https://developer.android.com/studio/releases/gradle-plugin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)를 참조하세요.

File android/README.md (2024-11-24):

# Android Apps

<p align="center">
  <span>English</span> |
  <a href="README.zh-CN.md">简体中文</a> |
  <a href="README.de-DE.md">Deutsch</a> |
  <a href="README.fr-FR.md">Français</a> |
  <a href="README.es-ES.md">Español</a> |
  <a href="README.ko-KR.md">한국어</a>
</p>

## Features

Click on the links below to read about the features of the apps.

- [Robot App](robot/README.md)
- [Controller App](controller/README.md)

## Install the apps

The easiest way to get either of the apps is to download it directly to the phone using the corresponding QR code. If you are on the phone browser, you can also just click on the QR code. You can then open the apk on your phone and [install](https://www.lifewire.com/install-apk-on-android-4177185) it. Note that the apk is only signed with a debug key.

<table style="width:100%;border:none;text-align:center">
  <tr>
    <td>  <a href="https://app.openbot.org/robot" target="_blank">
    🤖 App
  </a>
    </td>
    <td>
  <a href="https://app.openbot.org/controller" target="_blank">
    🎮 App
  </a>
      </td>
  </tr>
  <tr>
    <td>🤖 App</td>
    <td>🎮 App</td>
  </tr>
</table>

Alternatively, you can download the apks from the assets of any [release](https://github.com/intel-isl/OpenBot/releases). If you want the latest app from the master branch, you can also download it from the build artifacts [here](https://github.com/intel-isl/OpenBot/actions?query=workflow%3A%22Java+CI+with+Gradle%22). Note, that it may not be stable. If you would like to make changes to the app later, follow the steps below to compile the app and deploy it on your phone.

## Build the apps

### Prerequisites

- [Android Studio Electric Eel | 2022.1.1 or later](https://developer.android.com/studio/index.html) for building and installing the apks.
- Android device and Android development environment with minimum API 21.
- Currently, we use API 33 as compile SDK and API 32 as target SDK. It should get installed automatically, but if not you can install the SDK manually. Go to Android Studio -> Preferences -> Appearance & Behaviour -> System Settings -> Android SDK. Make sure API 33 is checked and click apply.

Android SDK

### Build process

1. Open Android Studio and select *Open an existing Android Studio project*.
2. Select the OpenBot/android directory and click OK.
3. If you want to install the [OpenBot app](app/README.md) make sure to select the *app* configuration. If you want to install the [Controller app](controller/README.md), select the *controller* configuration. Confirm Gradle Sync if neccessary. To perform a Gradle Sync manually, click on the gradle icon.
  Gradle Sync
4. Connect your Android device and make sure USB Debugging in the [developer options](https://developer.android.com/studio/debug/dev-options) is enabled. Depending on your development environment [further steps](https://developer.android.com/studio/run/device) might be necessary. You should see your device in the navigation bar at the top now.
  Phone
5. Click the Run button (the green arrow) or select Run > Run 'android' from the top menu. You may need to rebuild the project using Build > Rebuild Project.
  Run
6. If it asks you to use Instant Run, click *Proceed Without Instant Run*.

### Troubleshooting

#### Versions

If you get a message like `The project is using an incompatible version (AGP 7.4.0) of the Android Gradle plugin. Latest supported version is AGP 7.3.0` you need to upgrade Android Studio or downgrade your gradle plugin. You can read more about the version compatablility between Android Studio and the gradle plugin [here](https://developer.android.com/studio/releases/gradle-plugin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).

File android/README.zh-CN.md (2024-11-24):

# Android Apps

<p align="center">
  <a href="README.md">English</a> |
  <span>简体中文</span> |
  <a href="README.de-DE.md">Deutsch</a> |
  <a href="README.fr-FR.md">Français</a> |
  <a href="README.es-ES.md">Español</a> |
  <a href="README.ko-KR.md">한국어</a>
</p>

## 功能

点击下面的链接阅读应用程序的功能。

- [机器人应用](robot/README.md)
- [控制器应用](controller/README.md)

## 安装应用程序

获取应用程序的最简单方法是使用相应的二维码直接下载到手机上。如果你在手机浏览器上，也可以直接点击二维码。然后你可以在手机上打开apk并[安装](https://www.lifewire.com/install-apk-on-android-4177185)它。请注意，apk仅使用调试密钥签名。

<table style="width:100%;border:none;text-align:center">
  <tr>
    <td>  <a href="https://app.openbot.org/robot" target="_blank">
    🤖 App
  </a>
    </td>
    <td>
  <a href="https://app.openbot.org/controller" target="_blank">
    🎮 App
  </a>
      </td>
  </tr>
  <tr>
    <td>🤖 App</td>
    <td>🎮 App</td>
  </tr>
</table>

或者，你可以从任何[发布](https://github.com/intel-isl/OpenBot/releases)的资产中下载apk。如果你想要来自主分支的最新应用程序，你也可以从构建工件[这里](https://github.com/intel-isl/OpenBot/actions?query=workflow%3A%22Java+CI+with+Gradle%22)下载。请注意，它可能不稳定。如果你以后想对应用程序进行更改，请按照以下步骤编译应用程序并将其部署到手机上。

## 构建应用程序

### 先决条件

- [Android Studio Electric Eel | 2022.1.1或更高版本](https://developer.android.com/studio/index.html)用于构建和安装apk。
- Android设备和最低API 21的Android开发环境。
- 目前，我们使用API 33作为编译SDK和API 32作为目标SDK。它应该会自动安装，但如果没有，你可以手动安装SDK。进入Android Studio -> Preferences -> Appearance & Behaviour -> System Settings -> Android SDK。确保API 33已选中并点击应用。

Android SDK

### 构建过程

1. 打开Android Studio并选择*打开现有的Android Studio项目*。
2. 选择OpenBot/android目录并点击确定。
3. 如果你想安装[OpenBot应用](app/README.md)，请确保选择*app*配置。如果你想安装[控制器应用](controller/README.md)，请选择*controller*配置。如有必要，确认Gradle同步。要手动执行Gradle同步，请点击gradle图标。
  Gradle Sync
4. 连接你的Android设备，并确保在[开发者选项](https://developer.android.com/studio/debug/dev-options)中启用USB调试。根据你的开发环境，可能需要[进一步的步骤](https://developer.android.com/studio/run/device)。现在你应该可以在顶部的导航栏中看到你的设备。
  Phone
5. 点击运行按钮（绿色箭头）或从顶部菜单中选择运行 > 运行'android'。你可能需要使用构建 > 重建项目来重新构建项目。
  Run
6. 如果它要求你使用即时运行，请点击*继续不使用即时运行*。

### 故障排除

#### 版本

如果你收到类似`项目正在使用不兼容版本（AGP 7.4.0）的Android Gradle插件。最新支持的版本是AGP 7.3.0`的消息，你需要升级Android Studio或降级你的gradle插件。你可以在[这里](https://developer.android.com/studio/releases/gradle-plugin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)阅读更多关于Android Studio和gradle插件之间版本兼容性的信息。

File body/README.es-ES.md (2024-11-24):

# OpenBot: Cuerpo del Robot

<p align="center">
  <a href="README.md">English</a> |
  <a href="README.zh-CN.md">简体中文</a> |
  <a href="README.de-DE.md">Deutsch</a> |
  <a href="README.fr-FR.md">Français</a> |
  <span>Español</span> |
  <a href="README.ko-KR.md">한국어</a>
</p>

Puedes comprar un OpenBot [listo para usar (RTR)](rtr) en Amazon:
- [RTR-TT](https://buy.openbot.org/rtr-tt)
- [RTR-520](https://buy.openbot.org/rtr-520)

Para pedidos más grandes, por favor contáctanos por correo electrónico.

## Construyendo el tuyo propio

Puedes construir cualquier cuerpo de robot con ruedas alrededor de un microcontrolador como el Arduino Nano para usar con el conjunto de software de OpenBot. Hemos diseñado un [cuerpo impreso en 3D](diy) para un robot con ruedas que se basa en hardware de hobby de bajo costo y fácilmente disponible. [OpenBot Lite](lite) es una variante más pequeña y simplificada de la versión DIY de OpenBot desarrollada para la educación. Incluso si no deseas construirlo, puedes encontrar útiles las [guías en video paso a paso](lite/#step-by-step-video-guides). También hemos diseñado un [cuerpo impreso en 3D](rc_truck) para camiones RC 1:16 disponibles comercialmente (como [este](https://www.amazon.de/dp/B00M3J7DJW)). También proporcionamos planos para construir un [vehículo multi-terreno](mtv), como una plataforma de propósito general para proyectos al aire libre utilizando el marco de OpenBot.

A continuación, se presentan varios ejemplos con instrucciones de construcción y más detalles:

<table style="width:100%;border:none;text-align:center">
  <tr>
  <td>  <a href="diy">
    DIY
  </a>
  </td>
  <td>
  <a href="lite">
    Lite
  </a>
  </td>
  <td>
  <a href="rc_truck">
    RC Truck
  </a>
  </td>
  <td>
  <a href="mtv">
    Multi-Terrain Vehicle
  </a>
  </td>
  <td>
  <a href="rtr">
    RTR
  </a>
  </td>
  </tr>
  <tr>
    <td><a href="diy"> DIY </a></td>
    <td><a href="lite"> Lite </a></td>
    <td><a href="rc_truck"> RC Truck </a></td>
    <td><a href="mtv"> Vehículo Multi-Terreno </a></td>
    <td><a href="rtr"> RTR </a></td>
  </tr>
</table>

## Siguiente

Flashea el [Firmware de Arduino](../firmware/README.es-ES.md)

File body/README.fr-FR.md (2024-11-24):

# OpenBot : Corps de Robot

<p align="center">
  <a href="README.md">English</a> |
  <a href="README.zh-CN.md">简体中文</a> |
  <a href="README.de-DE.md">Deutsch</a> |
  <span>Français</span> |
  <a href="README.es-ES.md">Español</a> |
  <a href="README.ko-KR.md">한국어</a>
</p>

Vous pouvez acheter un OpenBot [prêt à l'emploi (RTR)](rtr) sur Amazon :
- [RTR-TT](https://buy.openbot.org/rtr-tt)
- [RTR-520](https://buy.openbot.org/rtr-520)

Pour des demandes de commandes plus importantes, veuillez nous contacter par email.

## Construire le vôtre

Vous pouvez construire n'importe quel robot à roues autour d'un microcontrôleur tel que l'Arduino Nano pour l'utiliser avec la pile logicielle OpenBot. Nous avons conçu un [corps imprimé en 3D](diy) pour un robot à roues qui repose sur du matériel de loisir peu coûteux et facilement disponible. [OpenBot Lite](lite) est une variante plus petite et simplifiée de la version DIY d'OpenBot développée pour l'éducation. Même si vous ne souhaitez pas le construire, vous pouvez trouver les [guides vidéo étape par étape](lite/#step-by-step-video-guides) utiles. Nous avons également conçu un [corps imprimé en 3D](rc_truck) pour des camions RC 1:16 disponibles dans le commerce (comme [celui-ci](https://www.amazon.de/dp/B00M3J7DJW)). Nous fournissons également des plans pour construire un [véhicule tout-terrain](mtv), en tant que plateforme polyvalente pour des projets extérieurs utilisant le cadre OpenBot.

Voici quelques exemples avec des instructions de construction et plus de détails :

<table style="width:100%;border:none;text-align:center">
  <tr>
  <td>  <a href="diy">
    DIY
  </a>
  </td>
  <td>
  <a href="lite">
    Lite
  </a>
  </td>
  <td>
  <a href="rc_truck">
    RC Truck
  </a>
  </td>
  <td>
  <a href="mtv">
    Multi-Terrain Vehicle
  </a>
  </td>
  <td>
  <a href="rtr">
    RTR
  </a>
  </td>
  </tr>
  <tr>
    <td><a href="diy"> DIY </a></td>
    <td><a href="lite"> Lite </a></td>
    <td><a href="rc_truck"> RC Truck </a></td>
    <td><a href="mtv"> Multi-Terrain Vehicle </a></td>
    <td><a href="rtr"> RTR </a></td>
  </tr>
</table>

## Ensuite

Flashez le [Firmware Arduino](../firmware/README.md)

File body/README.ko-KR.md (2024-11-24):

# OpenBot: 로봇 본체

<p align="center">
  <a href="README.md">English</a> |
  <a href="README.zh-CN.md">简体中文</a> |
  <a href="README.de-DE.md">Deutsch</a> |
  <a href="README.fr-FR.md">Français</a> |
  <a href="README.es-ES.md">Español</a> |
  <span>한국어</span>
</p>

아마존에서 [만들어진(RTR)](rtr) OpenBot을 구매할 수 있습니다:
- [RTR-TT](https://buy.openbot.org/rtr-tt)
- [RTR-520](https://buy.openbot.org/rtr-520)

대량 주문 요청은 이메일로 문의해 주세요.

## 직접 만들기

Arduino Nano와 같은 마이크로컨트롤러를 사용하여 OpenBot 소프트웨어 스택과 함께 사용할 수 있는 바퀴가 달린 로봇 본체를 만들 수 있습니다. 저희는 저비용의 쉽게 구할 수 있는 취미 하드웨어를 기반으로 한 [3D 프린팅 본체](diy)를 설계했습니다. [OpenBot Lite](lite)는 교육용으로 개발된 OpenBot DIY 버전의 소형 및 간소화된 변형입니다. 직접 만들고 싶지 않더라도 [단계별 비디오 가이드](lite/#step-by-step-video-guides)가 유용할 수 있습니다. 또한 상업적으로 판매되는 1:16 RC 트럭(예: [이 제품](https://www.amazon.de/dp/B00M3J7DJW))을 위한 [3D 프린팅 본체](rc_truck)도 설계했습니다. OpenBot 프레임워크를 사용한 야외 프로젝트를 위한 범용 플랫폼으로 [다목적 차량](mtv) 제작을 위한 청사진도 제공합니다.

아래는 제작 지침 및 추가 세부 정보가 포함된 여러 예시입니다:

<table style="width:100%;border:none;text-align:center">
  <tr>
  <td>  <a href="diy">
    DIY
  </a>
  </td>
  <td>
  <a href="lite">
    Lite
  </a>
  </td>
  <td>
  <a href="rc_truck">
    RC 트럭
  </a>
  </td>
  <td>
  <a href="mtv">
    다목적 차량
  </a>
  </td>
  <td>
  <a href="rtr">
    RTR
  </a>
  </td>
  </tr>
  <tr>
    <td><a href="diy"> DIY </a></td>
    <td><a href="lite"> Lite </a></td>
    <td><a href="rc_truck"> RC 트럭 </a></td>
    <td><a href="mtv"> 다목적 차량 </a></td>
    <td><a href="rtr"> RTR </a></td>
  </tr>
</table>

## 다음

[Arduino 펌웨어](../../firmware/README.ko-KR.md)를 플래시하세요!

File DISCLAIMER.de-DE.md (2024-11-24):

## HAFTUNGSAUSSCHLUSS

<p align="center">
  <a href="DISCLAIMER.md">English</a> |
  <a href="DISCLAIMER.zh-CN.md">简体中文</a> |
  <span>Deutsch</span> |
  <a href="DISCLAIMER.fr-FR.md">Français</a> |
  <a href="DISCLAIMER.es-ES.md">Español</a> |
  <a href="DISCLAIMER.ko-KR.md">한국어</a>
</p>

Das OpenBot-Projekt ist eine Open-Source-Initiative, die darauf abzielt, zugängliche Robotiklösungen für Bildungs-, Experimentier- und Freizeitzwecke bereitzustellen. Der folgende Haftungsausschluss beschreibt die Nutzungsbedingungen für die OpenBot-Software und Hardware-Designs.

### Software-Haftungsausschluss

- Die OpenBot-Software wird ohne jegliche ausdrückliche oder stillschweigende Gewährleistung bereitgestellt.
- Die Mitwirkenden und Betreuer des OpenBot-Projekts sind nicht verantwortlich für Schäden oder Datenverluste, die durch die Nutzung der Software entstehen können.
- Die Benutzer sind dafür verantwortlich, sicherzustellen, dass ihre Nutzung der OpenBot-Software allen relevanten Gesetzen und Vorschriften entspricht.
- Der Missbrauch der Software für böswillige oder unethische Zwecke ist strengstens untersagt.

### Hardware-Haftungsausschluss

- Die OpenBot-Hardware-Designs werden zu Bildungs- und Experimentierzwecken bereitgestellt und sind möglicherweise nicht für alle Anwendungsfälle geeignet.
- Die Benutzer sind dafür verantwortlich, sicherzustellen, dass ihre Implementierung der OpenBot-Hardware den Sicherheitsstandards und Vorschriften ihrer Region entspricht.
- Die Mitwirkenden und Betreuer des OpenBot-Projekts haften nicht für Verletzungen, Schäden oder Verluste, die durch den Bau, die Modifikation oder den Betrieb von Robotern auf Basis der OpenBot-Hardware-Designs entstehen.
- Die Benutzer werden aufgefordert, Vorsicht walten zu lassen und die Sicherheit zu priorisieren, wenn sie Roboter auf Basis von OpenBot bauen und betreiben.

### Allgemeiner Haftungsausschluss

- Die Mitwirkenden und Betreuer des OpenBot-Projekts lehnen jegliche Haftung für Schäden oder Verluste ab, die direkt oder indirekt aus der Nutzung oder dem Missbrauch der OpenBot-Software und Hardware-Designs entstehen.
- Die Benutzer werden ermutigt, die OpenBot-Ressourcen verantwortungsbewusst, ethisch und in Übereinstimmung mit allen geltenden Gesetzen und Vorschriften zu nutzen.

Durch die Nutzung der OpenBot-Software und Hardware-Designs erkennen Sie an, dass Sie die Bedingungen dieses Haftungsausschlusses gelesen, verstanden und akzeptiert haben.

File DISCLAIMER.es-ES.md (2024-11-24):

## AVISO LEGAL

<p align="center">
  <a href="DISCLAIMER.md">English</a> |
  <a href="DISCLAIMER.zh-CN.md">简体中文</a> |
  <a href="DISCLAIMER.de-DE.md">Deutsch</a> |
  <a href="DISCLAIMER.fr-FR.md">Français</a> |
  <span>Español</span> |
  <a href="DISCLAIMER.ko-KR.md">한국어</a>
</p>

El proyecto OpenBot es una iniciativa de código abierto que tiene como objetivo proporcionar soluciones robóticas accesibles para fines educativos, experimentales y recreativos. El siguiente aviso legal describe los términos y condiciones de uso del software y los diseños de hardware de OpenBot.

### Aviso Legal del Software

- El software de OpenBot se proporciona "tal cual" sin ninguna garantía de ningún tipo, expresa o implícita.
- Los colaboradores y mantenedores del proyecto OpenBot no son responsables de ningún daño o pérdida de datos que pueda resultar del uso del software.
- Los usuarios son responsables de asegurarse de que su uso del software de OpenBot cumpla con todas las leyes y regulaciones relevantes.
- El uso indebido del software para fines maliciosos o poco éticos está estrictamente prohibido.

### Aviso Legal del Hardware

- Los diseños de hardware de OpenBot se proporcionan para fines educativos y experimentales y pueden no ser adecuados para todos los casos de uso.
- Los usuarios son responsables de asegurarse de que su implementación del hardware de OpenBot cumpla con los estándares de seguridad y regulaciones aplicables a su región.
- Los colaboradores y mantenedores del proyecto OpenBot no son responsables de ninguna lesión, daño o pérdida resultante de la construcción, modificación u operación de robots basados en los diseños de hardware de OpenBot.
- Se insta a los usuarios a actuar con precaución y priorizar la seguridad al construir y operar robots basados en OpenBot.

### Aviso Legal General

- Los colaboradores y mantenedores del proyecto OpenBot declinan cualquier responsabilidad por daños o pérdidas incurridas directa o indirectamente por el uso o mal uso del software y los diseños de hardware de OpenBot.
- Se anima a los usuarios a utilizar los recursos de OpenBot de manera responsable, ética y en cumplimiento con todas las leyes y regulaciones aplicables.

Al usar el software y los diseños de hardware de OpenBot, usted reconoce que ha leído, entendido y aceptado los términos de este aviso legal.

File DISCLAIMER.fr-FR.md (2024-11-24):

## AVERTISSEMENT

<p align="center">
  <a href="DISCLAIMER.md">English</a> |
  <a href="DISCLAIMER.zh-CN.md">简体中文</a> |
  <a href="DISCLAIMER.de-DE.md">Deutsch</a> |
  <span>Français</span> |
  <a href="DISCLAIMER.es-ES.md">Español</a> |
  <a href="DISCLAIMER.ko-KR.md">한국어</a>
</p>

Le projet OpenBot est une initiative open-source visant à fournir des solutions robotiques accessibles à des fins éducatives, expérimentales et récréatives. Le présent avertissement décrit les termes et conditions d'utilisation des logiciels et des conceptions matérielles d'OpenBot.

### Avertissement sur le logiciel

- Le logiciel OpenBot est fourni "tel quel" sans aucune garantie, expresse ou implicite.
- Les contributeurs et mainteneurs du projet OpenBot ne sont pas responsables des dommages ou pertes de données pouvant résulter de l'utilisation du logiciel.
- Les utilisateurs sont responsables de s'assurer que leur utilisation du logiciel OpenBot est conforme à toutes les lois et réglementations en vigueur.
- L'utilisation abusive du logiciel à des fins malveillantes ou contraires à l'éthique est strictement interdite.

### Avertissement sur le matériel

- Les conceptions matérielles d'OpenBot sont fournies à des fins éducatives et expérimentales et peuvent ne pas convenir à tous les cas d'utilisation.
- Les utilisateurs sont responsables de s'assurer que leur mise en œuvre du matériel OpenBot est conforme aux normes de sécurité et aux réglementations applicables dans leur région.
- Les contributeurs et mainteneurs du projet OpenBot ne sont pas responsables des blessures, dommages ou pertes résultant de la construction, modification ou utilisation de robots basés sur les conceptions matérielles d'OpenBot.
- Les utilisateurs sont invités à faire preuve de prudence et à prioriser la sécurité lors de la construction et de l'utilisation de robots basés sur OpenBot.

### Avertissement général

- Les contributeurs et mainteneurs du projet OpenBot déclinent toute responsabilité pour les dommages ou pertes encourus directement ou indirectement par l'utilisation ou la mauvaise utilisation des logiciels et conceptions matérielles d'OpenBot.
- Les utilisateurs sont encouragés à utiliser les ressources d'OpenBot de manière responsable, éthique et en conformité avec toutes les lois et réglementations applicables.

En utilisant les logiciels et conceptions matérielles d'OpenBot, vous reconnaissez avoir lu, compris et accepté les termes de cet avertissement.

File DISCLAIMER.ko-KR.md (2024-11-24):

## 면책 조항

<p align="center">
  <a href="DISCLAIMER.md">English</a> |
  <a href="DISCLAIMER.zh-CN.md">简体中文</a> |
  <a href="DISCLAIMER.de-DE.md">Deutsch</a> |
  <a href="DISCLAIMER.fr-FR.md">Français</a> |
  <a href="DISCLAIMER.es-ES.md">Español</a> |
  <span>한국어</span>
</p>

OpenBot 프로젝트는 교육, 실험 및 오락 목적으로 접근 가능한 로봇 솔루션을 제공하는 오픈 소스 이니셔티브입니다. 다음 면책 조항은 OpenBot 소프트웨어 및 하드웨어 설계의 사용 조건을 설명합니다.

### 소프트웨어 면책 조항

- OpenBot 소프트웨어는 어떠한 종류의 보증 없이 "있는 그대로" 제공됩니다.
- OpenBot 프로젝트의 기여자 및 유지 관리자는 소프트웨어 사용으로 인해 발생할 수 있는 데이터 손실이나 손해에 대해 책임지지 않습니다.
- 사용자는 OpenBot 소프트웨어 사용이 모든 관련 법률 및 규정을 준수하는지 확인할 책임이 있습니다.
- 소프트웨어를 악의적이거나 비윤리적인 목적으로 잘못 사용하는 것은 엄격히 금지됩니다.

### 하드웨어 면책 조항

- OpenBot 하드웨어 설계는 교육 및 실험 목적으로 제공되며 모든 사용 사례에 적합하지 않을 수 있습니다.
- 사용자는 OpenBot 하드웨어의 구현이 해당 지역의 안전 기준 및 규정을 준수하는지 확인할 책임이 있습니다.
- OpenBot 프로젝트의 기여자 및 유지 관리자는 OpenBot 하드웨어 설계를 기반으로 한 로봇의 건설, 수정 또는 작동으로 인해 발생하는 부상, 손상 또는 손실에 대해 책임지지 않습니다.
- 사용자는 OpenBot 기반 로봇을 구축하고 운영할 때 주의를 기울이고 안전을 최우선으로 할 것을 권장합니다.

### 일반 면책 조항

- OpenBot 프로젝트의 기여자 및 유지 관리자는 OpenBot 소프트웨어 및 하드웨어 설계의 사용 또는 오용으로 인해 직접적 또는 간접적으로 발생하는 손해 또는 손실에 대한 책임을 부인합니다.
- 사용자는 OpenBot 리소스를 책임감 있게, 윤리적으로, 모든 적용 가능한 법률 및 규정을 준수하여 사용할 것을 권장합니다.

OpenBot 소프트웨어 및 하드웨어 설계를 사용함으로써, 귀하는 이 면책 조항의 내용을 읽고 이해하며 동의했음을 인정합니다.

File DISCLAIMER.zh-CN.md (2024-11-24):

## 免责声明

<p align="center">
  <a href="DISCLAIMER.md">English</a> |
  <span>简体中文</span> |
  <a href="DISCLAIMER.de-DE.md">Deutsch</a> |
  <a href="DISCLAIMER.fr-FR.md">Français</a> |
  <a href="DISCLAIMER.es-ES.md">Español</a> |
  <a href="DISCLAIMER.ko-KR.md">한국어</a>
</p>

OpenBot 项目是一个开源计划，旨在为教育、实验和娱乐目的提供可访问的机器人解决方案。以下免责声明概述了 OpenBot 软件和硬件设计的使用条款和条件。

### 软件免责声明

- OpenBot 软件按“原样”提供，不提供任何明示或暗示的保证。
- OpenBot 项目的贡献者和维护者不对使用该软件可能导致的任何损坏或数据丢失负责。
- 用户有责任确保其使用 OpenBot 软件符合所有相关法律和法规。
- 严禁将软件用于恶意或不道德的目的。

### 硬件免责声明

- OpenBot 硬件设计仅供教育和实验用途，可能不适用于所有使用场景。
- 用户有责任确保其实施的 OpenBot 硬件符合其所在地区适用的安全标准和法规。
- OpenBot 项目的贡献者和维护者不对基于 OpenBot 硬件设计的机器人在构建、修改或操作过程中导致的任何伤害、损坏或损失负责。
- 用户在构建和操作基于 OpenBot 的机器人时应谨慎行事，并优先考虑安全。

### 一般免责声明

- OpenBot 项目的贡献者和维护者对因直接或间接使用或误用 OpenBot 软件和硬件设计而导致的任何损害或损失不承担任何责任。
- 鼓励用户负责任地、道德地使用 OpenBot 资源，并遵守所有适用的法律和法规。

通过使用 OpenBot 软件和硬件设计，您确认您已阅读、理解并同意本免责声明的条款。

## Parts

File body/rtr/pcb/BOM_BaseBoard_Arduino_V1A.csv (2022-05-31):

ID | Name | Designator | Footprint | Quantity | Manufacturer Part | Manufacturer | Supplier | Supplier Part | Price
1 | LESD5D5.0CT1G | D3,D4 | SOD-523_L1.2-W0.8-LS1.6-BI | 2 | LESD5D5.0CT1G | Leshan Radio | LCSC | C383211 | 0.018
2 | B2B-PH-K-S(LF)(SN) | CN5,CN6,CN7,CN8 | CONN-TH_B2B-PH-K-S | 4 | B2B-PH-K-S(LF)(SN) | JST | LCSC | C131337 | 0.035
3 | 1.25T-1-10AW | CN3 | CONN-TH_10P-P1.25-H_1.25T-1-10AW | 1 | 1.25T-1-10AW | BOOMELE | LCSC | C10840 | 0.049
4 | Header-Male-2.54_2x3 | J2,J3,J5,J4 | HDR-TH_6P-P2.54-V-R2-C3-S2.54 | 4 | Header-Male-2.54_2x3 | BOOMELE | LCSC | C65114 | 0.031
5 | 1.25T-1-3A | CN1,CN2 | CONN-TH_3P-P1.25_1.25T-1-3A | 2 | 1.25T-1-3A | BOOMELE | LCSC | C10820 | 0.017
6 | 1.25T-6A | CN4 | CONN-TH_1.25T-6A | 1 | - | Boom Precision Elec | LCSC | C145974 | 0.033
7 | 10K | R15,R3 | R0402 | 2 | AR02BTC1002 | Viking Tech | LCSC | C317926 | 0.026
8 | 210S-1*2P L=11.6MMGold-plated black | H1 | HDR-TH_2P-P2.54-V | 1 | 210S-1*2P L=11.6MMGold-plated black | Ckmtw | LCSC | C124375 | 0.027
9 | 30K | R1 | R0402 | 1 | AR02BTD3002 | Viking Tech | LCSC | C319654 | 0.032
10 | 1K | R11,R12,R13,R14 | R0402 | 4 | 0402WGJ0102TCE | UniOhm | LCSC | C25543 | 0.001
11 | 100nF | C1 | C0603 | 1 | CC0603KRX7R9BB104 | YAGEO | LCSC | C14663 | 0.002
12 | 10K | R2,R4,R9,R10,R7,R8,R6,R5 | R0402 | 8 | SY0402FN10KP | SANYEAR | LCSC | C380740 | 0.001
13 | 10uF | C2 | C1206 | 1 | CL31A106KBHNNNE | SAMSUNG | LCSC | C13585 | 0.036
14 | S8050_C2146 | Q2,Q5,Q4,Q3 | SOT-23-3_L3.0-W1.7-P0.95-LS2.9-BR | 4 | S8050 | CJ | LCSC | C2146 | 0.019
15 | SMAJ13A_C309856 | D2 | SMA_L4.3-W2.6-LS5.2-RD | 1 | SMAJ13A | Brightking Elec (TAIWAN) | LCSC | C309856 | 0.051
16 | AO3409A | Q1 | SOT-23-3_L3.0-W1.7-P0.95-LS2.9-BR | 1 | AO3409A | Youtai Semiconductor Co., Ltd. | LCSC | C347496 | 0.043
17 | 1N5819HW1-7-F | D1 | SOD-123F_L2.8-W1.8-LS3.7-RD | 1 | 1N5819HW1-7-F | DIODES | LCSC | C117948 | 0.142
18 | LM393DT | U1,U2 | SOIC-8_L5.0-W4.0-P1.27-LS6.0-BL | 2 | LM393DT | STMicroelectronics | LCSC | C32901 | 0.106
19 | Arduino_Nano_Header | J1 | DIP-30_L43.18-W15.24-ARDUINONANO | 1
20 | 210S-2*5P L=11.6MMGold-plated black | H2,H3 | HDR-TH_10P-P2.54-V-R2-C5-S2.54_MTP125-1205S1 | 2 | 210S-2*5P L=11.6MMGold-plated black | Ckmtw | LCSC | C124387 | 0.079
21 | DC-044B-3A-2.0 | DC1 | DC-IN-TH_DC-044B-3A-2.00 | 1 | DC-044B-3A-2.0 | XKB Enterprise | LCSC | C388627 | 0.271

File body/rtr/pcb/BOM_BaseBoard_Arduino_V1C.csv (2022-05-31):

ID | Name | Designator | Footprint | Quantity | Manufacturer Part | Manufacturer | Supplier | Supplier Part | Price
1 | LESD5D5.0CT1G | D3,D4 | SOD-523_L1.2-W0.8-LS1.6-BI | 2 | LESD5D5.0CT1G | Leshan Radio | LCSC | C383211 | 0.018
2 | 1.25T-1-10AW | CN13 | CONN-TH_10P-P1.25-H_1.25T-1-10AW | 1 | 1.25T-1-10AW | BOOMELE | LCSC | C10840 | 0.049
3 | Header-Male-2.54_2x3 | J1,J2,J3,J4 | HDR-TH_6P-P2.54-V-R2-C3-S2.54 | 4 | Header-Male-2.54_2x3 | BOOMELE | LCSC | C65114 | 0.031
4 | 10K | R7,R8,R9,R10,R11,R12,R16,R17,R18,R26 | R0402 | 10 | SY0402FN10KP | SANYEAR | LCSC | C380740 | 0.001
5 | 1K | R23,R24,R19,R25 | R0603 | 4 | 0603WAJ0102T5E | UniOhm | LCSC | C25585 | 0.001
6 | AMS1117-5.0 | U5 | SOT-223_L6.5-W3.5-P2.30-LS7.0-BR | 1 | AMS1117-5.0 | AMS | LCSC | C6187 | 0.193
7 | S8050_C2146 | Q1,Q3,Q4,Q2 | SOT-23-3_L3.0-W1.7-P0.95-LS2.9-BR | 4 | S8050 | CJ | LCSC | C2146 | 0.019
8 | AO3409A | Q5 | SOT-23-3_L3.0-W1.7-P0.95-LS2.9-BR | 1 | AO3409A | Youtai Semiconductor Co., Ltd. | LCSC | C347496 | 0.043
9 | 1K | R5,R6,R13,R14,R20,R21,R22 | R0402 | 7 | 0402WGJ0102TCE | UniOhm | LCSC | C25543 | 0.001
10 | LM393DT | U3,U4 | SOIC-8_L5.0-W4.0-P1.27-LS6.0-BL | 2 | LM393DT | STMicroelectronics | LCSC | C32901 | 0.106
11 | 1uF | C6,C12,C8 | C0402 | 3 | CL05A105KO5NNNC | SAMSUNG | LCSC | C29266 | 0.003
12 | 10K | R3 | R0402 | 1 | 0402WGF1002TCE | UniOhm | LCSC | C25744 | 0.001
13 | 0.1 | R1,R2 | R1206 | 2 | PE1206FRF470R1L | YAGEO | LCSC | C309528 | 0.064
14 | 30K | R15 | R0402 | 1 | RMC040230K1%N | Tyohm | LCSC | C325409 | 0.002
15 | 100nF | C1,C3 | C0603 | 2 | CC0603KRX7R9BB104 | YAGEO | LCSC | C14663 | 0.002
16 | 100nF | C10 | C0402 | 1 | CC0402ZRY5V7BB104P | YAGEO | LCSC | C327414
17 | 100uF | C2,C4 | CAP-TH_BD6.3-P2.50-D1.0-FD | 2 | RXW101M1EBK-0611 | LELON | LCSC | C134637 | 0.078
18 | 16MHz | X1 | OSC-SMD_4P-L2.5-W2.0-BL | 1 | S2216000091080 | JGHC | LCSC | C426966 | 0.14
19 | 9pF | C9,C11 | C0402 | 2 | CC0402CRNPO9BN9R0 | YAGEO | LCSC | C282242 | 0.002
20 | 20K | R4 | R0402 | 1 | 0402WGF2002TCE | UniOhm | LCSC | C25765 | 0.001
21 | 4.7uF | C7 | CAP-SMD_L3.2-W1.6 | 1 | TC211A475M016Y | Sunlord | LCSC | C128333 | 0.118
22 | DRV8870DDAR | U1,U2 | HSOP-8_L5.0-W4.0-P1.27-LS6.2-BL-EP | 2 | DRV8870DDAR | TI | LCSC | C86590 | 0.731
23 | 1N5819HW1-7-F | D1 | SOD-123F_L2.8-W1.8-LS3.7-RD | 1 | 1N5819HW1-7-F | DIODES | LCSC | C117948 | 0.142
24 | B2B-PH-K-S(LF)(SN) | CN8,CN7,CN6,CN5,CN3,CN4,CN2,CN1 | CONN-TH_B2B-PH-K-S | 8 | B2B-PH-K-S(LF)(SN) | JST | LCSC | C131337 | 0.035
25 | 100nF | C5 | C0402 | 1 | CC0402MRY5V8BB104 | YAGEO | LCSC | C327271 | 0.003
26 | ATMEGA328P-AU | U6 | TQFP-32_L7.0-W7.0-P0.80-LS9.0-BL | 1 | ATMEGA328P-AU | MICROCHIP | LCSC | C14877 | 32.641
27 | TS-1088C-02526 | SW1 | SW-SMD_L4.0-W2.9-P4.15-EH | 1 | TS-1088C-02526 | XUNPU | LCSC | C455279 | 0.055
28 | 210S-1*2P L=11.6MMGold-plated black | H1 | HDR-TH_2P-P2.54-V | 1 | 210S-1*2P L=11.6MMGold-plated black | Ckmtw | LCSC | C124375 | 0.027
29 | LTST-C191KSKT | LED4 | LED0603-RD | 1 | LTST-C191KSKT | LITEON | LCSC | C125100 | 0.024
30 | LTST-C191KRKT | LED1 | LED0603-RD | 1 | LTST-C191KRKT | LITEON | LCSC | C125099 | 0.016
31 | LTST-C191KGKT | LED3,LED2 | LED0603-RD | 2 | LTST-C191KGKT | LITEON | LCSC | C125098 | 0.017
32 | 210S-2*3P L=11.6MMGold-plated black | H2 | HDR-TH_6P-P2.54-V-R2-C3-S2.54 | 1 | 210S-2*3P L=11.6MMGold-plated black | Ckmtw | LCSC | C124384 | 0.039
33 | SMAJ13A_C309856 | D2 | SMA_L4.3-W2.6-LS5.2-RD | 1 | SMAJ13A | Brightking Elec (TAIWAN) | LCSC | C309856 | 0.051
34 | DC-044B-3A-2.0 | DC1 | DC-IN-TH_DC-044B-3A-2.00 | 1 | DC-044B-3A-2.0 | XKB Enterprise | LCSC | C388627 | 0.271
35 | 1.25T-1-3A | CN9,CN10 | CONN-TH_3P-P1.25_1.25T-1-3A | 2 | 1.25T-1-3A | BOOMELE | LCSC | C10820 | 0.017
36 | 1.25T-6A | CN12 | CONN-TH_1.25T-6A | 1 | - | Boom Precision Elec | LCSC | C145974 | 0.033

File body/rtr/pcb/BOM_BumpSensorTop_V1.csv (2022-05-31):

ID | Name | Designator | Footprint | Quantity | Manufacturer Part | Manufacturer | Supplier | Supplier Part | Price
1 | 1.8K | R1 | R0603 | 1 | RC0603FR-071K8L | YAGEO | LCSC | C185354 | 0.001
2 | TS6620CJ | SW1 | SW-TH_4P-L6.0-W6.0-P4.50-LS6.5 | 1 | TS6620CJ | SHOU HAN | LCSC | C393949 | 0.028
3 | 1.25T-1-3AW | CN1 | CONN-TH_1.25T-1-3AW | 1 | 1.25T-1-3AW | BOOMELE | LCSC | C10833 | 0.017

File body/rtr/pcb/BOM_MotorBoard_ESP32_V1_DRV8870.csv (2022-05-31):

ID | Name | Designator | Footprint | Quantity | Manufacturer Part | Manufacturer | Supplier | Supplier Part | Price
1 | 210S-2*6P L=11.6MMGold-plated black | H1 | HDR-TH_12P-P2.54-V-R2-C6-S2.54 | 1 | 210S-2*6P L=11.6MMGold-plated black | Ckmtw | LCSC | C124388 | 0.081
2 | DRV8870DDAR | U2,U1 | HSOP-8_L5.0-W4.0-P1.27-LS6.2-BL-EP | 2 | DRV8870DDAR | TI | LCSC | C86590 | 0.731
3 | 0 | R2 | R0402 | 1 | RC0402JR-070RL | YAGEO | LCSC | C60485 | 0.001
4 | B6B-PH-K-S(LF)(SN) | CN1,CN2 | CONN-TH_B6B-PH-K-S | 2 | B6B-PH-K-S(LF)(SN) | JST | LCSC | C131342 | 0.068
5 | 0.1 | R1,R4 | R1206 | 2 | PE1206FRF470R1L | YAGEO | LCSC | C309528 | 0.064
6 | 100nF | C3,C1 | C0603 | 2 | CC0603KRX7R9BB104 | YAGEO | LCSC | C14663 | 0.002
7 | 100uF | C4,C2 | CAP-TH_BD6.3-P2.50-D1.0-FD | 2 | RXW101M1EBK-0611 | LELON | LCSC | C134637 | 0.078
8 | 10K | R3 | R0402 | 1 | RC0402JR-0710KL | YAGEO | LCSC | C60489 | 0.001

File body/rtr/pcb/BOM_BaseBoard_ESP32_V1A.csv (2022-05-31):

ID | Name | Designator | Footprint | Quantity | Manufacturer Part | Manufacturer | Supplier | Supplier Part | Price
1 | LESD5D5.0CT1G | D3,D4 | SOD-523_L1.2-W0.8-LS1.6-BI | 2 | LESD5D5.0CT1G | Leshan Radio | LCSC | C383211 | 0.018
2 | B2B-PH-K-S(LF)(SN) | CN6,CN7,CN8,CN5 | CONN-TH_B2B-PH-K-S | 4 | B2B-PH-K-S(LF)(SN) | JST | LCSC | C131337 | 0.035
3 | ESP32-DEVKITC-32D_ESP32-DEVKITC-32D | U2 | MODULE_ESP32-DEVKITC-32D | 1
4 | 1.25T-1-10AW | CN4 | CONN-TH_10P-P1.25-H_1.25T-1-10AW | 1 | 1.25T-1-10AW | BOOMELE | LCSC | C10840 | 0.049
5 | SY8120B1ABC | U1 | SOT-23-6_L2.9-W1.6-P0.95-LS2.8-BL | 1 | SY8120B1ABC | Silergy | LCSC | C88474 | 0.348
6 | 1K | R9,R7,R8,R10 | R0402 | 4 | 0402WGJ0102TCE | UniOhm | LCSC | C25543 | 0.001
7 | SMAJ13A_C309856 | D2 | SMA_L4.3-W2.6-LS5.2-RD | 1 | SMAJ13A | Brightking Elec (TAIWAN) | LCSC | C309856 | 0.051
8 | 210S-1*2P L=11.6MMGold-plated black | H1 | HDR-TH_2P-P2.54-V | 1 | 210S-1*2P L=11.6MMGold-plated black | Ckmtw | LCSC | C124375 | 0.027
9 | 100K | R2 | R0402 | 1 | 0402WGF1003TCE | UniOhm | LCSC | C25741 | 0.001
10 | 1N5819HW1-7-F | D1 | SOD-123F_L2.8-W1.8-LS3.7-RD | 1 | 1N5819HW1-7-F | DIODES | LCSC | C117948 | 0.142
11 | Header-Female-2.54_2x6 | H4,H8 | HDR-TH_12P-P2.54-V-R2-C6-S2.54 | 2 | Header-Female-2.54_2x6 | BOOMELE | LCSC | C36191 | 0.075
12 | 10K | R4 | R0402 | 1 | AR02BTC1002 | Viking Tech | LCSC | C317926 | 0.026
13 | 10K | R6,R3,R11 | R0402 | 3 | 0402WGJ0103TCE | UniOhm | LCSC | C25531 | 0.001
14 | 13.7K | R5 | R0402 | 1 | 0402WGF1372TCE | UniOhm | LCSC | C25854 | 0.001
15 | 10uF | C2 | C0805 | 1 | CL21A106KAYNNNF | Samsung Electro-Mechanics | LCSC | C337995 | 0.02
16 | 22uF | C5,C4 | C0805 | 2 | CL21A226MPQNNNE | SAMSUNG | LCSC | C29277 | 0.017
17 | 30K | R1 | R0402 | 1 | AR02BTD3002 | Viking Tech | LCSC | C319654 | 0.032
18 | S8050_C2146 | Q3,Q4,Q2,Q1 | SOT-23-3_L3.0-W1.7-P0.95-LS2.9-BR | 4 | S8050 | CJ | LCSC | C2146 | 0.019
19 | 100nF | C1 | C0402 | 1 | CC0402MRY5V8BB104 | YAGEO | LCSC | C327271 | 0.003
20 | 22pF | C3 | C0402 | 1 | GRM1552C1H220JA01D | MuRata | LCSC | C85935 | 0.002
21 | DC-044B-3A-2.0 | DC1,DC2 | DC-IN-TH_DC-044B-3A-2.00 | 2 | DC-044B-3A-2.0 | XKB Enterprise | LCSC | C388627 | 0.271
22 | 1.25T-6A | CN1 | CONN-TH_1.25T-6A | 1 | - | Boom Precision Elec | LCSC | C145974 | 0.033
23 | 1.25T-1-3A | CN2,CN3 | CONN-TH_3P-P1.25_1.25T-1-3A | 2 | 1.25T-1-3A | BOOMELE | LCSC | C10820 | 0.017
24 | 4.7uH | L1 | IND-SMD_L4.0-W4.0_ABG04A30 | 1 | ABG04A30M4R7 | COILANK INTERNATIONAL | LCSC | C253572 | 0.076

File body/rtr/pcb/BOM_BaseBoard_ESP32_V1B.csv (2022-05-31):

ID | Name | Designator | Footprint | Quantity | Manufacturer Part | Manufacturer | Supplier | Supplier Part | Price
1 | LESD5D5.0CT1G | D3,D4 | SOD-523_L1.2-W0.8-LS1.6-BI | 2 | LESD5D5.0CT1G | Leshan Radio | LCSC | C383211 | 0.018
2 | ESP32-DEVKITC-32D_ESP32-DEVKITC-32D | U2 | MODULE_ESP32-DEVKITC-32D | 1
3 | 1.25T-1-10AW | CN8 | CONN-TH_10P-P1.25-H_1.25T-1-10AW | 1 | 1.25T-1-10AW | BOOMELE | LCSC | C10840 | 0.049
4 | S8050_C2146 | Q2,Q3,Q4,Q1 | SOT-23-3_L3.0-W1.7-P0.95-LS2.9-BR | 4 | S8050 | CJ | LCSC | C2146 | 0.019
5 | 10K | R6,R3,R11 | R0402 | 3 | 0402WGJ0103TCE | UniOhm | LCSC | C25531 | 0.001
6 | 1N5819HW1-7-F | D1 | SOD-123F_L2.8-W1.8-LS3.7-RD | 1 | 1N5819HW1-7-F | DIODES | LCSC | C117948 | 0.142
7 | SY8120B1ABC | U1 | SOT-23-6_L2.9-W1.6-P0.95-LS2.8-BL | 1 | SY8120B1ABC | Silergy | LCSC | C88474 | 0.348
8 | DRV8870DDAR | U3,U4,U5,U6 | HSOP-8_L5.0-W4.0-P1.27-LS6.2-BL-EP | 4 | DRV8870DDAR | TI | LCSC | C86590 | 0.731
9 | 30K | R2 | R0402 | 1 | AR02BTD3002 | Viking Tech | LCSC | C319654 | 0.032
10 | 1K | R13,R12,R14,R15 | R0402 | 4 | 0402WGJ0102TCE | UniOhm | LCSC | C25543 | 0.001
11 | B6B-PH-K-S(LF)(SN) | CN2,CN4,CN5,CN3 | CONN-TH_B6B-PH-K-S | 4 | B6B-PH-K-S(LF)(SN) | JST | LCSC | C131342 | 0.068
12 | SMAJ13A_C309856 | D2 | SMA_L4.3-W2.6-LS5.2-RD | 1 | SMAJ13A | Brightking Elec (TAIWAN) | LCSC | C309856 | 0.051
13 | 100nF | C6,C8,C10,C12 | C0603 | 4 | CC0603KRX7R9BB104 | YAGEO | LCSC | C14663 | 0.002
14 | 10uF | C5 | C0805 | 1 | CL21A106KAYNNNF | Samsung Electro-Mechanics | LCSC | C337995 | 0.02
15 | B2B-PH-K-S(LF)(SN) | CN12,CN11,CN9,CN10 | CONN-TH_B2B-PH-K-S | 4 | B2B-PH-K-S(LF)(SN) | JST | LCSC | C131337 | 0.035
16 | 10K | R5 | R0402 | 1 | AR02BTC1002 | Viking Tech | LCSC | C317926 | 0.026
17 | 22uF | C3,C4 | C0805 | 2 | CL21A226MPQNNNE | SAMSUNG | LCSC | C29277 | 0.017
18 | 22pF | C2 | C0402 | 1 | GRM1552C1H220JA01D | MuRata | LCSC | C85935 | 0.002
19 | 100uF | C7,C9,C11,C13 | CAP-TH_BD6.3-P2.50-D1.0-FD | 4 | RXW101M1EBK-0611 | LELON | LCSC | C134637 | 0.078
20 | 13.7K | R4 | R0402 | 1 | 0402WGF1372TCE | UniOhm | LCSC | C25854 | 0.001
21 | 0.1 | R8,R9,R10,R7 | R1206 | 4 | PE1206FRF470R1L | YAGEO | LCSC | C309528 | 0.064
22 | 100K | R1 | R0402 | 1 | 0402WGF1003TCE | UniOhm | LCSC | C25741 | 0.001
23 | 210S-1*2P L=11.6MMGold-plated black | H2 | HDR-TH_2P-P2.54-V | 1 | 210S-1*2P L=11.6MMGold-plated black | Ckmtw | LCSC | C124375 | 0.027
24 | 100nF | C1 | C0402 | 1 | CC0402MRY5V8BB104 | YAGEO | LCSC | C327271 | 0.003
25 | DC-044B-3A-2.0 | DC1,DC2 | DC-IN-TH_DC-044B-3A-2.00 | 2 | DC-044B-3A-2.0 | XKB Enterprise | LCSC | C388627 | 0.271
26 | 1.25T-6A | CN1 | CONN-TH_1.25T-6A | 1 | - | Boom Precision Elec | LCSC | C145974 | 0.033
27 | 1.25T-1-3A | CN6,CN7 | CONN-TH_3P-P1.25_1.25T-1-3A | 2 | 1.25T-1-3A | BOOMELE | LCSC | C10820 | 0.017
28 | 4.7uH | L1 | IND-SMD_L4.0-W4.0_ABG04A30 | 1 | ABG04A30M4R7 | COILANK INTERNATIONAL | LCSC | C253572 | 0.076

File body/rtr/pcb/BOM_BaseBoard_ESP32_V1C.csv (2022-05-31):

ID | Name | Designator | Footprint | Quantity | Manufacturer Part | Manufacturer | Supplier | Supplier Part | Price
1 | LESD5D5.0CT1G | D3,D4 | SOD-523_L1.2-W0.8-LS1.6-BI | 2 | LESD5D5.0CT1G | Leshan Radio | LCSC | C383211 | 0.018
2 | 100nF | C1,C6,C8,C10,C11,C12,C13 | C0402 | 7 | CC0402MRY5V8BB104 | YAGEO | LCSC | C327271 | 0.003
3 | 1uF | C7 | C0402 | 1 | CL05A105KO5NNNC | SAMSUNG | LCSC | C29266 | 0.003
4 | 1N5819HW1-7-F | D1 | SOD-123F_L2.8-W1.8-LS3.7-RD | 1 | 1N5819HW1-7-F | DIODES | LCSC | C117948 | 0.142
5 | 210S-1*2P L=11.6MMGold-plated black | H2 | HDR-TH_2P-P2.54-V | 1 | 210S-1*2P L=11.6MMGold-plated black | Ckmtw | LCSC | C124375 | 0.027
6 | 4.7uH | L1 | IND-SMD_L4.0-W4.0_ABG04A30 | 1 | ABG04A30M4R7 | COILANK INTERNATIONAL | LCSC | C253572 | 0.076
7 | 10K | R1,R16 | R0402 | 2 | SY0402FN10KP | SANYEAR | LCSC | C380740 | 0.001
8 | 13.7K | R5 | R0402 | 1 | 0402WGF1372TCE | UniOhm | LCSC | C25854 | 0.001
9 | SY8120B1ABC | U1 | SOT-23-6_L2.9-W1.6-P0.95-LS2.8-BL | 1 | SY8120B1ABC | Silergy | LCSC | C88474 | 0.348
10 | AMS1117-3.3 | U3 | SOT-223-3_L6.5-W3.4-P2.30-LS7.0-BR | 1 | AMS1117-3.3 | AMS | LCSC | C6186 | 0.15
11 | 1.25T-1-10AW | CN5 | CONN-TH_10P-P1.25-H_1.25T-1-10AW | 1 | 1.25T-1-10AW | BOOMELE | LCSC | C10840 | 0.049
12 | DRV8870DDAR | U4,U7,U5,U6 | HSOP-8_L5.0-W4.0-P1.27-LS6.2-BL-EP | 4 | DRV8870DDAR | TI | LCSC | C86590 | 0.731
13 | B6B-PH-K-S(LF)(SN) | CN4,CN3,CN1,CN2 | CONN-TH_B6B-PH-K-S | 4 | B6B-PH-K-S(LF)(SN) | JST | LCSC | C131342 | 0.068
14 | 100nF | C16,C20,C14,C18 | C0603 | 4 | CC0603KRX7R9BB104 | YAGEO | LCSC | C14663 | 0.002
15 | 100uF | C17,C21,C15,C19 | CAP-TH_BD6.3-P2.50-D1.0-FD | 4 | RXW101M1EBK-0611 | LELON | LCSC | C134637 | 0.078
16 | S8050_C2146 | Q4,Q5,Q7,Q6 | SOT-23-3_L3.0-W1.7-P0.95-LS2.9-BR | 4 | S8050 | CJ | LCSC | C2146 | 0.019
17 | 100K | R3 | R0402 | 1 | 0402WGF1003TCE | UniOhm | LCSC | C25741 | 0.001
18 | 30K | R12 | R0402 | 1 | RMC040230K1%N | Tyohm | LCSC | C325409 | 0.002
19 | SMAJ13A_C309856 | D2 | SMA_L4.3-W2.6-LS5.2-RD | 1 | SMAJ13A | Brightking Elec (TAIWAN) | LCSC | C309856 | 0.051
20 | 10uF | C5 | C0805 | 1 | CL21A106KAYNNNF | Samsung Electro-Mechanics | LCSC | C337995 | 0.02
21 | LTST-C191KRKT | LED1 | LED0603-RD | 1 | LTST-C191KRKT | LITEON | LCSC | C125099 | 0.016
22 | TS-1088C-02526 | SW2,SW1 | SW-SMD_L4.0-W2.9-P4.15-EH | 2 | TS-1088C-02526 | XUNPU | LCSC | C455279 | 0.055
23 | 22uF | C4,C3 | C0805 | 2 | CL21A226MPQNNNE | SAMSUNG | LCSC | C29277 | 0.017
24 | 22pF | C2 | C0402 | 1 | GRM1552C1H220JA01D | MuRata | LCSC | C85935 | 0.002
25 | 10K | R14,R2,R24 | R0402 | 3 | 0402WGJ0103TCE | UniOhm | LCSC | C25531 | 0.001
26 | 1K | R15 | R0603 | 1 | 0603WAJ0102T5E | UniOhm | LCSC | C25585 | 0.001
27 | 0.1 | R20,R21,R18,R19 | R1206 | 4 | PE1206FRF470R1L | YAGEO | LCSC | C309528 | 0.064
28 | 1K | R26,R25,R22,R23 | R0402 | 4 | 0402WGJ0102TCE | UniOhm | LCSC | C25543 | 0.001
29 | B2B-PH-K-S(LF)(SN) | CN6,CN7,CN12,CN13 | CONN-TH_B2B-PH-K-S | 4 | B2B-PH-K-S(LF)(SN) | JST | LCSC | C131337 | 0.035
30 | 22uF | C9 | C0603 | 1 | CL10A226MQ8NRNC | SAMSUNG | LCSC | C59461 | 0.005
31 | DC-044B-3A-2.0 | DC1,DC2 | DC-IN-TH_DC-044B-3A-2.00 | 2 | DC-044B-3A-2.0 | XKB Enterprise | LCSC | C388627 | 0.271
32 | 1.25T-6A | CN8 | CONN-TH_1.25T-6A | 1 | - | Boom Precision Elec | LCSC | C145974 | 0.033
33 | 1.25T-1-3A | CN9,CN10 | CONN-TH_3P-P1.25_1.25T-1-3A | 2 | 1.25T-1-3A | BOOMELE | LCSC | C10820 | 0.017
34 | ESP32-WROOM-32UE(4MB) | U2 | WIFI-SMD_ESP32-WROOM-32UE | 1 | ESP32-WROOM-32UE(4MB) | Espressif Systems | LCSC | C701344 | 3.08

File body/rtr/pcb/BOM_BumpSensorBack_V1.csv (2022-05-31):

ID | Name | Designator | Footprint | Quantity | Manufacturer Part | Manufacturer | Supplier | Supplier Part | Price
1 | 8.2K | R1 | R0603 | 1 | RC0603FR-078K2L | YAGEO | LCSC | C114637 | 0.001
2 | 6.8K | R2 | R0603 | 1 | RC0603FR-076K8L | YAGEO | LCSC | C114632 | 0.001
3 | 1.25T-1-3A | CN1,CN2 | CONN-TH_3P-P1.25_1.25T-1-3A | 2 | 1.25T-1-3A | BOOMELE | LCSC | C10820 | 0.017
4 | 10nF | C1,C2 | C0603 | 2 | CC0603KRX7R9BB103 | YAGEO | LCSC | C100042 | 0.002
5 | TS6620CJ | SW1,SW2 | SW-TH_4P-L6.0-W6.0-P4.50-LS6.5 | 2 | TS6620CJ | SHOU HAN | LCSC | C393949 | 0.028

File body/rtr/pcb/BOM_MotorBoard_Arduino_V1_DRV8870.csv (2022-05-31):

ID | Name | Designator | Footprint | Quantity | Manufacturer Part | Manufacturer | Supplier | Supplier Part | Price
1 | DRV8870DDAR | U1 | HSOP-8_L5.0-W4.0-P1.27-LS6.2-BL-EP | 1
2 | 10K | R2,R4 | R0402 | 2
3 | 100nF | C1,C3 | C0603 | 2
4 | B2B-PH-K-S(LF)(SN) | CN1,CN2 | CONN-TH_B2B-PH-K-S | 2
5 | 100uF | C2 | CAP-TH_BD6.3-P2.50-D1.0-FD | 1
6 | 20K | R3 | R0402 | 1
7 | 0.1 | R1 | R1206 | 1
8 | INA181A1IDBVT | U2 | SOT-23-6_L2.9-W1.6-P0.95-LS2.8-BR | 1
9 | DS1023-2*5SF11 | H1 | HDR-TH_10P-P2.54-V-R2-C5-S2.54 | 1

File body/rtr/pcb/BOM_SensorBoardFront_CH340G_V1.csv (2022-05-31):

ID | Name | Designator | Footprint | Quantity | Manufacturer Part | Manufacturer | Supplier | Supplier Part | Price
1 | 3K | R6 | R0603 | 1 | RC0603FR-073KL | YAGEO | LCSC | C126358 | 0.001
2 | 2.4K | R7 | R0603 | 1 | RC0603FR-072K4L | YAGEO | LCSC | C114611 | 0.001
3 | 1.25T-1-3A | CN2,CN3 | CONN-TH_3P-P1.25_1.25T-1-3A | 2 | 1.25T-1-3A | BOOMELE | LCSC | C10820 | 0.017
4 | LESD5D5.0CT1G | D2,D3,D4 | SOD-523_L1.2-W0.8-LS1.6-BI | 3 | LESD5D5.0CT1G | Leshan Radio | LCSC | C383211 | 0.018
5 | RCWL-9600 | U2 | SOP-16_L10.0-W3.9-P1.27-LS6.0-TL | 1 | RCWL-9600 | RCWL |  | RCWL-9600
6 | TYPE-C-31-M-12 | USBC1 | USB-C_SMD-TYPE-C-31-M-12 | 1 | TYPE-C-31-M-12 | Rectangular Connectors - Contacts | LCSC | C165948 | 0.249
7 | 100nF | C10,C11,C12 | C0402 | 3 | CC0402ZRY5V7BB104P | YAGEO | LCSC | C327414
8 | 12pF | C13,C14 | C0402 | 2 | CC0402JRNPO9BN120 | YAGEO | LCSC | C106201 | 0.001
9 | 1.25T-10A | CN4 | CONN-TH_1.25T-10A | 1 | - | Boom Precision Elec | LCSC | C145978 | 0.048
10 | BAT760-7 | D1 | SOD-323_L1.8-W1.3-LS2.5-RD | 1 | BAT760-7 | DIODES | LCSC | C124187 | 0.057
11 | 10K | R8,R11 | R0402 | 2 | 0402WGJ0103TCE | UniOhm | LCSC | C25531 | 0.001
12 | 5.1K | R9,R10 | R0402 | 2 | 0402WGJ0512TCE | UniOhm | LCSC | C25941 | 0.001
13 | CH340G | U3 | SOIC-16_L9.9-W3.9-P1.27-LS6.0-BL | 1 | CH340G | WCH | LCSC | C14267 | 0.462
14 | 12MHz | X1 | OSC-SMD_4P-L2.5-W2.0-BL | 1 | S22120001210120 | JGHC | LCSC | C479184 | 0.132
15 | 10nF | C3,C7,C8,C9 | C0603 | 4 | CC0603KRX7R9BB103 | YAGEO | LCSC | C100042 | 0.002
16 | S8050_C2146 | Q2,Q1 | SOT-23-3_L3.0-W1.7-P0.95-LS2.9-BR | 2 | S8050 | CJ | LCSC | C2146 | 0.019
17 | XC6206P332MR_C347376 | U1 | SOT-23-3_L3.0-W1.7-P0.95-LS2.9-BR | 1 | XC6206P332MR | Youtai Semiconductor Co., Ltd. | LCSC | C347376 | 0.027
18 | 75K | R3,R5 | R0603 | 2 | 0603WAF7502T5E | UniOhm | LCSC | C23242 | 0.001
19 | 470pF | C1,C2 | C0603 | 2 | CL10B471KB8NNNC | SAMSUNG | LCSC | C22396 | 0.005
20 | 1uF | C5,C6,C4 | C0603 | 3 | CL10A105KP8NNNC | SAMSUNG | LCSC | C26413 | 0.004
21 | 1.25T-1-3AW | CN1 | CONN-TH_1.25T-1-3AW | 1 | 1.25T-1-3AW | BOOMELE | LCSC | C10833 | 0.017
22 | 10K | R1,R2 | R0603 | 2 | 0603WAJ0103T5E | UniOhm | LCSC | C15401 | 0.001
23 | 2.2K | R4 | R0603 | 1 | WR06X2201FTL | WALSIN | LCSC | C163872 | 0.001
24 | TS6620CJ | SW1,SW2 | SW-TH_4P-L6.0-W6.0-P4.50-LS6.5 | 2 | TS6620CJ | SHOU HAN | LCSC | C393949 | 0.028
25 | RCWL-1640-A-X-T | LS1 | RCWL-1640 | 1 | RCWL-1640-A-X-T | RCWL | RCWL | RCWL-1640-A-X-T
26 | RCWL-1640-A-X-R | LS2 | RCWL-1640 | 1 | RCWL-1640-A-X-R | RCWL | RCWL | RCWL-1640-A-X-R

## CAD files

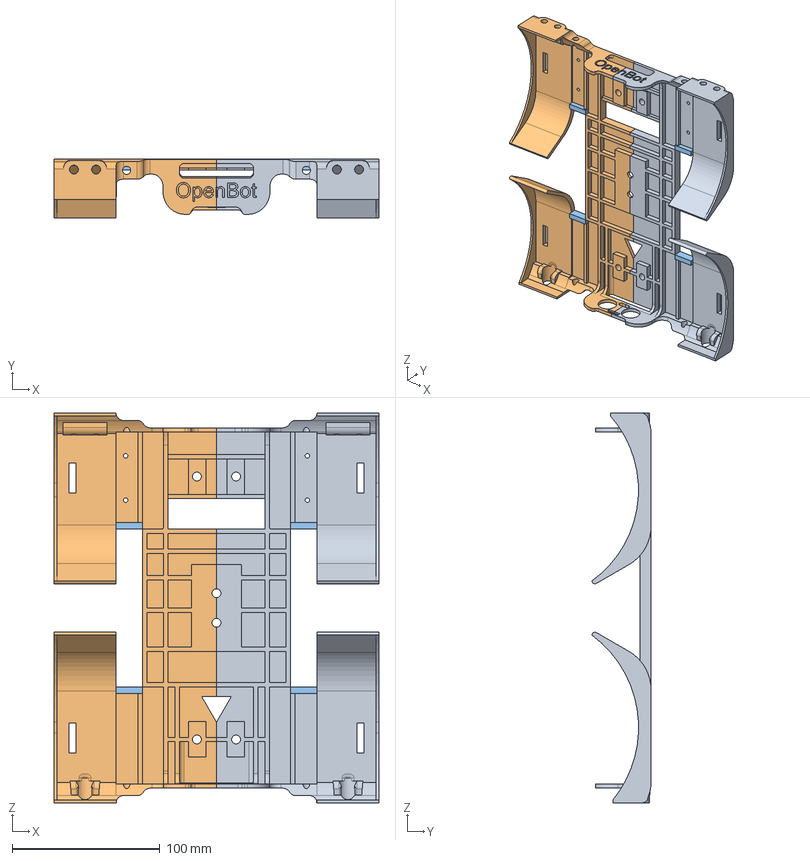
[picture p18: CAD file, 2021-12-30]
body/rc_truck/cad/rc_truck_body/main_frame.step
220.0 x 40.0 x 264.0 mm

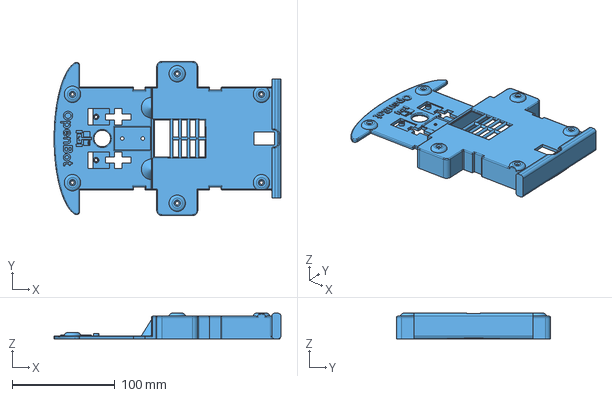
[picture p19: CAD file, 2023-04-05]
body/diy/cad/block_body/block_body_top_big.step
221.0 x 150.0 x 25.0 mm

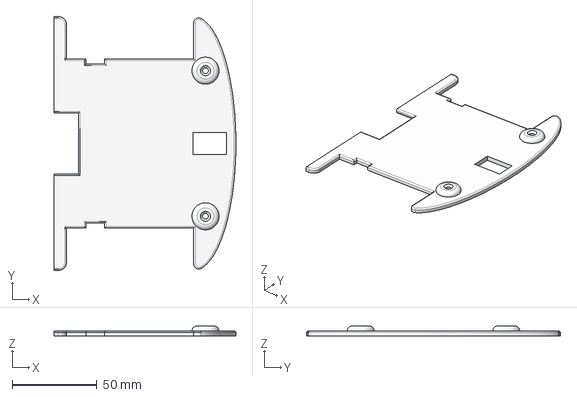
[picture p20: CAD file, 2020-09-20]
body/diy/cad/glue_body/glue_body_top_B.step
107.3 x 150.0 x 6.00 mm

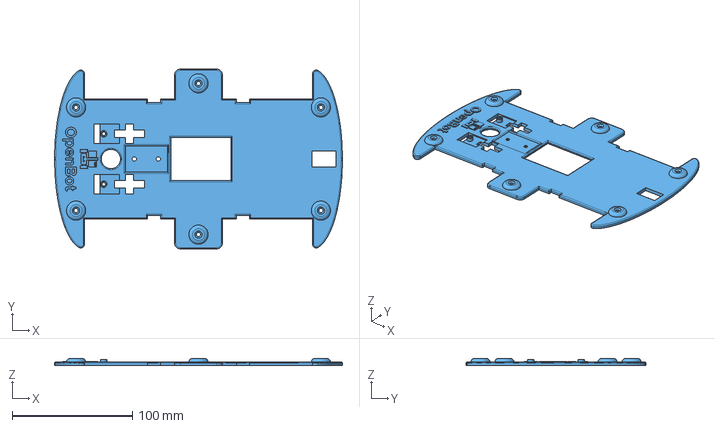
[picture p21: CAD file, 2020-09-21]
body/diy/cad/regular_body/body_top.step
240.0 x 150.0 x 6.00 mm

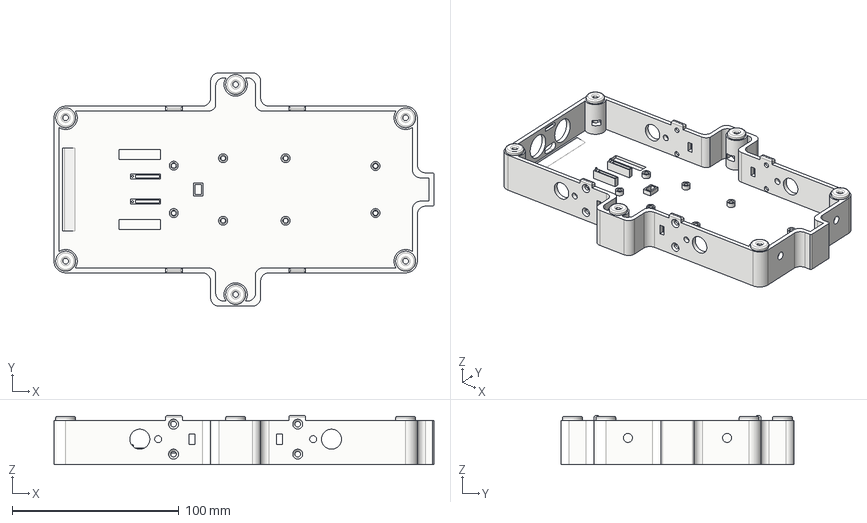
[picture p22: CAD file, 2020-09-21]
body/diy/cad/slim_body/slim_body_bottom.step
228.0 x 140.0 x 29.5 mm

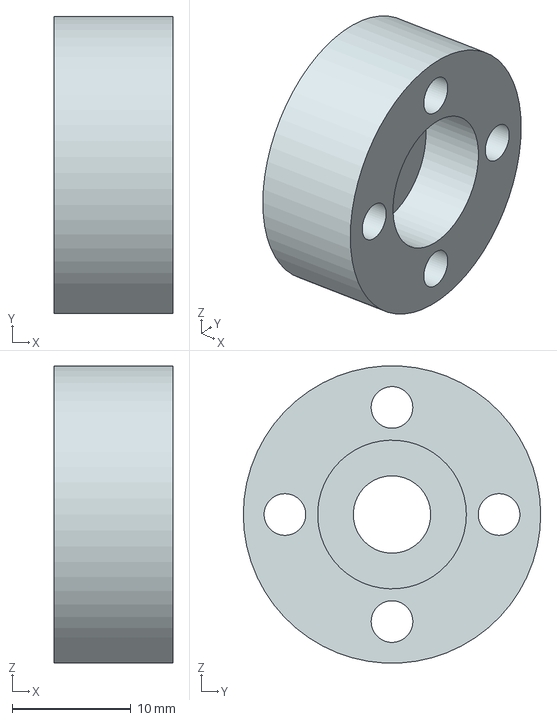
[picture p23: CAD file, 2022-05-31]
body/mtv/cad/BearingCover/BearingCover.step
10.0 x 25.0 x 25.0 mm

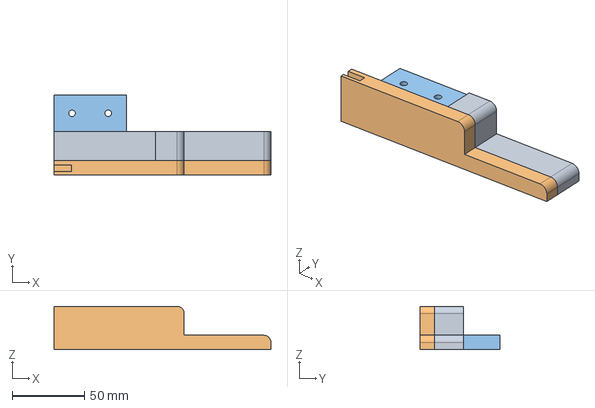
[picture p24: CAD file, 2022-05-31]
body/mtv/cad/Buffer/Buffer_Right.step
150.0 x 55.0 x 30.0 mm

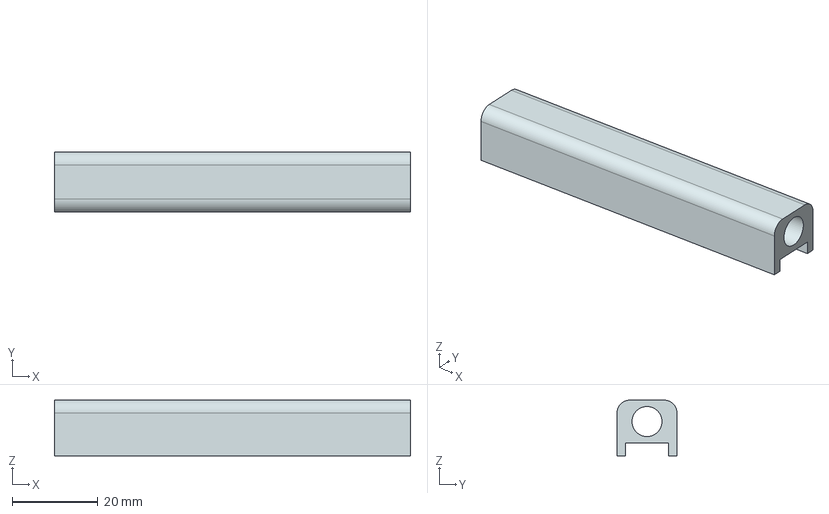
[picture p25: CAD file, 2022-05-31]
body/mtv/cad/Compartment/Compartment_Battery_Mount-P1.step
83.0 x 14.0 x 13.0 mm

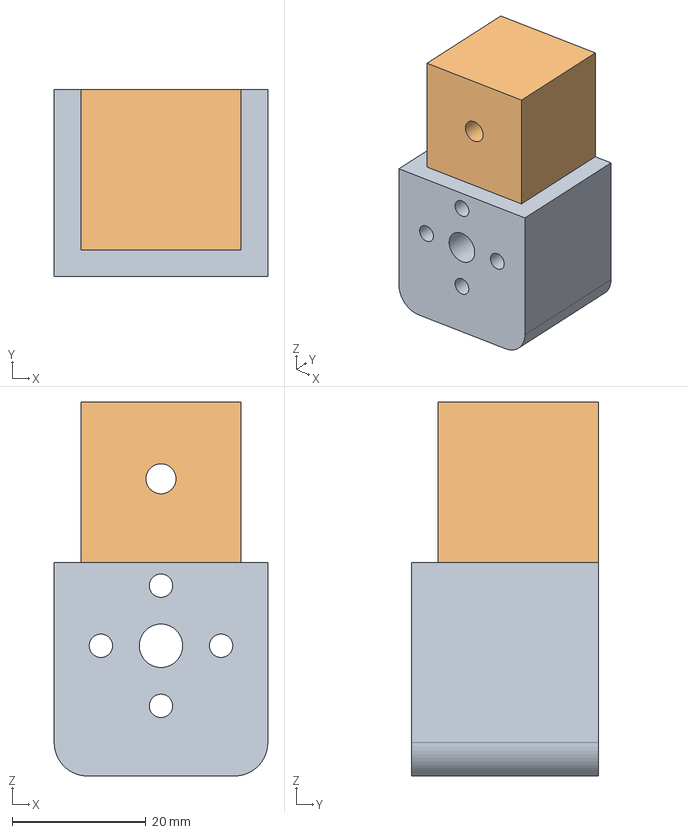
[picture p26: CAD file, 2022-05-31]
body/mtv/cad/Joints/End_Joint.step
32.0 x 28.0 x 56.0 mm

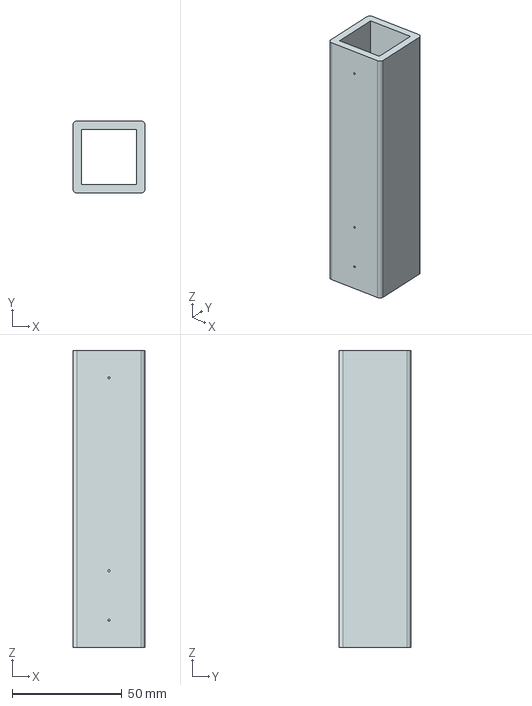
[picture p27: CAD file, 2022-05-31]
body/mtv/cad/Legs/Rear_Leg.step
33.0 x 33.0 x 135.5 mm

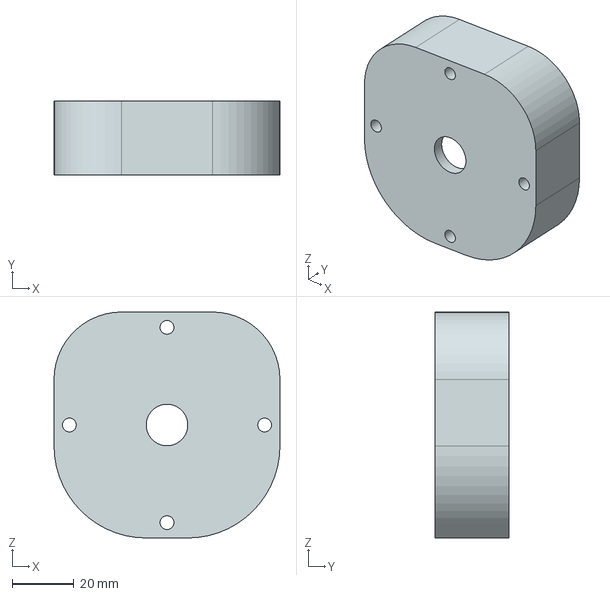
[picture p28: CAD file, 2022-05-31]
body/mtv/cad/MotorAssembly/MotorEnclosure_Bottom.step
73.5 x 24.0 x 73.5 mm

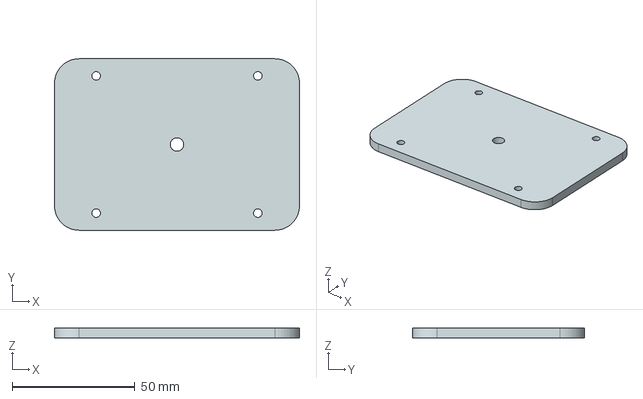
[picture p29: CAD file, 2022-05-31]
body/mtv/cad/PhoneMount/Phone_Mount.step
100.0 x 70.0 x 4.00 mm

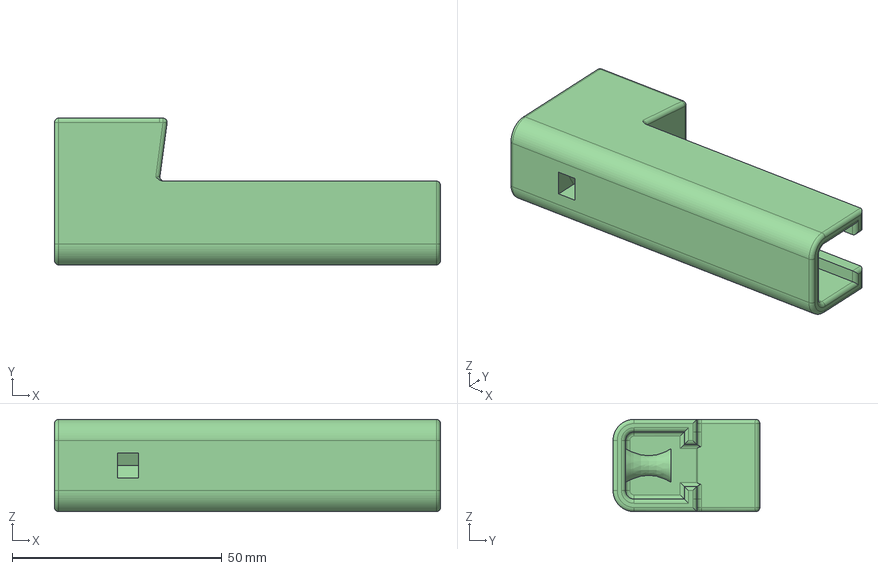
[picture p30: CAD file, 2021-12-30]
body/phone_mount/phone_mount_bottom.step
92.0 x 35.0 x 22.0 mm

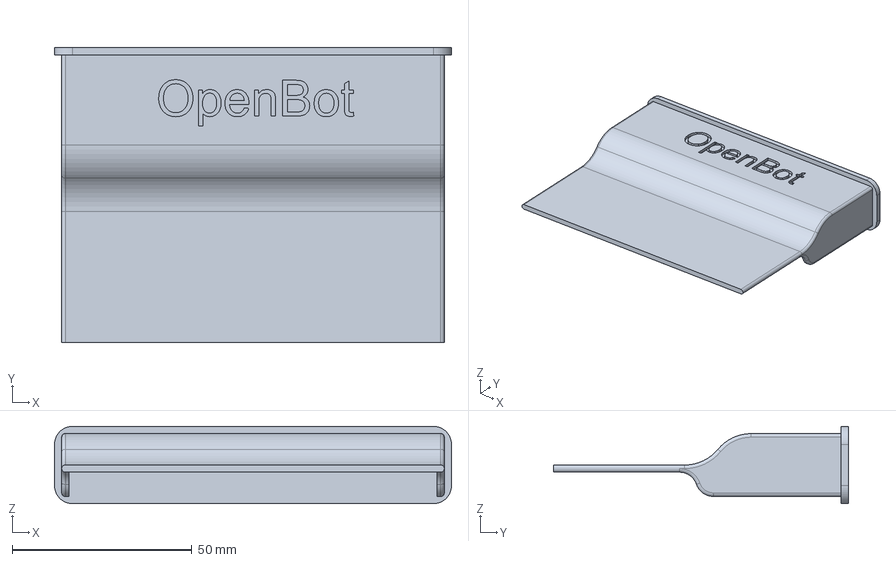
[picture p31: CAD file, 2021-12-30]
body/rc_truck/cad/rc_truck_body/side_cover.step
110.5 x 82.0 x 21.5 mm

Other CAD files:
body/phone_mount_bottom.step
body/rtr/cad/rtr_mount.step
body/diy/cad/block_body/block_body_top_big_lego.step
body/diy/cad/glue_body/glue_body_top_A.step
body/body_bottom.step
body/body_top.step
body/diy/cad/block_body/block_body_bottom.step
body/diy/cad/block_body/block_body_bottom.stl
body/diy/cad/block_body/block_body_top.step
body/diy/cad/block_body/block_body_top.stl
body/diy/cad/block_body/block_body_top_big.stl
body/diy/cad/block_body/block_body_top_big_lego.stl
body/diy/cad/block_body/block_body_top_lego.step
body/diy/cad/block_body/block_body_top_lego.stl
body/diy/cad/glue_body/glue_body_bottom_A.step
body/diy/cad/glue_body/glue_body_bottom_A.stl
body/diy/cad/glue_body/glue_body_bottom_B.step
body/diy/cad/glue_body/glue_body_bottom_B.stl
body/diy/cad/glue_body/glue_body_top_A.stl
body/diy/cad/glue_body/glue_body_top_B.stl
body/diy/cad/glue_body/glue_connector_bottom.step
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

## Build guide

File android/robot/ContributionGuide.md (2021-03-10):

# Contribution Guide

The application codebase follows a single activity architecture. 

It launches with `MainActivity.java` which holds `MainFragment.java` as it's default fragment. 

`MainFragment.java` has a recyclerview which is used to route to different screens and features using Android's Navigation component. The recycler view adapter is loaded with data curated from `FeatureList.java` class.

The project contains two `abstract` classes `ControlsFragment.java` and `CameraFragment.java` which can be extended to inherit the relvevant functionalities.

#### `ControlsFragment.java`

This class contains all relevant code required to operate the robot via a controller. Just extending this class will give your feature the ability to control the robot in one go. It uses two `private` methods,

```
private void processKeyEvent(KeyEvent keyCode)
```

and 

```
private void handlePhoneControllerEvents()
```

 to process game controller, and  phone controller key actions, and pass the processed String data to 
`protected abstract void processControllerKeyData(String data)` which is exposed to inheriting classes, which can be used to update the UI accordingly. 

#### `CameraFragment.java`

This class uses CameraX API to enable camera preview in the app. It extends the functionality of `ControlsFragment.java` to support robot connection and integration by default. 

To add camera preview to your feature:

1. Replace `extends Fragment`  with `extends CameraFragment` like this:

   	`public class AIFragment extends CameraFragment`
   
2. To overlay your own UI over this camera preview, `CameraFragment.java` offers two protected methods.

   	a.) `View inflateFragment(ViewBinding viewBinding, LayoutInflater inflater, ViewGroup container)`
   	b.) `View inflateFragment(int resId, LayoutInflater inflater, ViewGroup container)`

    Depending on whether you use ViewBinding or resource file to inflate your view, use the relevant method, and in the `onCreateView` method of your fragment, return it like this:

    ```
    @Override
    public View onCreateView(
        @NotNull LayoutInflater inflater, ViewGroup container, Bundle savedInstanceState) {
      // Inflate the layout for this fragment
      binding = FragmentAiBinding.inflate(inflater, container, false);
    
      return inflateFragment(binding, inflater, container);
    }
    ```
    or
    ```
     @Override
     public View onCreateView(
         @NotNull LayoutInflater inflater, ViewGroup container, Bundle savedInstanceState) {
        // Inflate the layout for this fragment
        View mView = inflater.inflate(R.layout.fragment_ai, container, false);
        
        return inflateFragment(mView, inflater, container);
     }
    ```
## To add a new feature:

1. Create a new fragment and it's respective layout file.

2. Depending on whether camera preview is needed or not, extend either of `ControlsFragment.java` or `CameraFragment.java` class.

3. Based on the category and subcategory this feature falls in, add it in `FeatureList.java`, along with it's title, icon and color. Here's an example for the same.

   ```
   ArrayList<SubCategory> subCategories = new ArrayList<>();
   subCategories.add(new SubCategory(DEFAULT, R.drawable.openbot_icon, "#4B7BFF"));
   subCategories.add(new SubCategory(FREE_ROAM, R.drawable.ic_game, "#FFFF6D00"));
   subCategories.add(new SubCategory(DATA_COLLECTION, R.drawable.ic_storage, "#93C47D"));
   subCategories.add(new SubCategory(AI_MODELS, R.drawable.ic_person_search, "#FFD966"));
   categories.add(new Category(ALL, subCategories));
   ```

3. In `nav_graph.xml`, using the Design Editor, add your fragment to the graph, and link in with `mainFragment`.

4. Finally, inside switch block in `onItemClick` method of `MainFragment.java` , add your feature title as a new case and navigate to the screen using it's action id like this.

   ```
   Navigation.findNavController(requireView())
       .navigate(R.id.action_mainFragment_to_AIFragment);
   ```

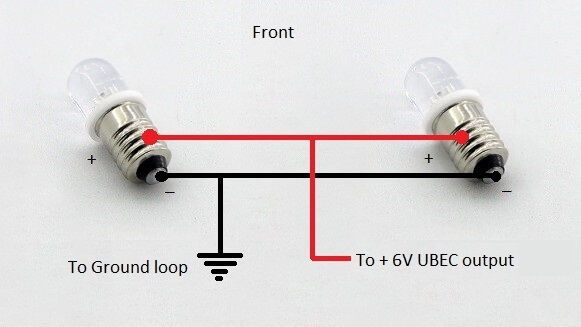
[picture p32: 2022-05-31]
docs/images/MTV/led-lamp-wiring.jpg

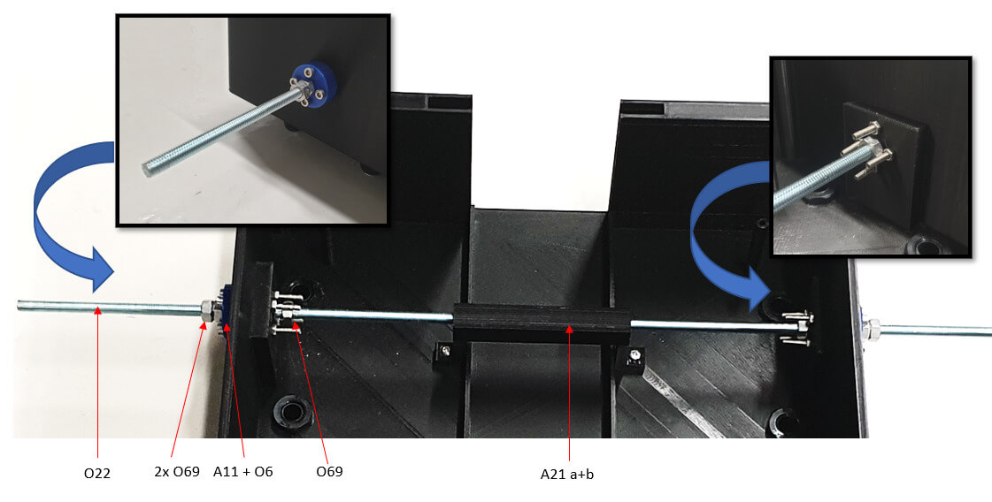
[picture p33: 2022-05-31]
docs/images/MTV/Assembly.jpg

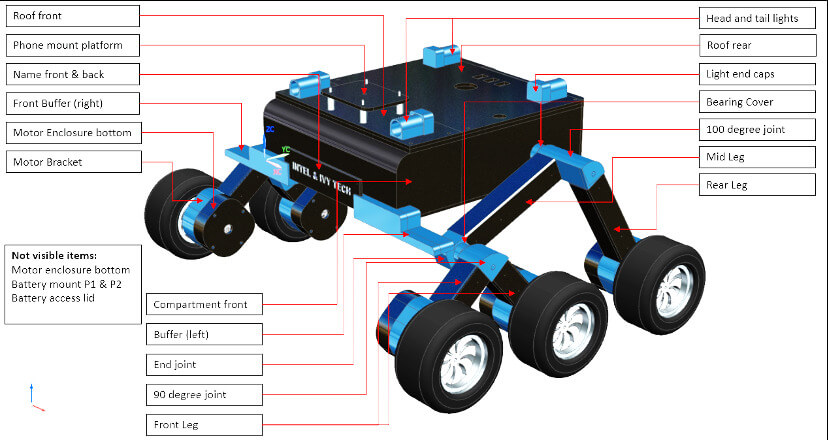
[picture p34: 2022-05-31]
docs/images/MTV/CAD_Assembly.jpg

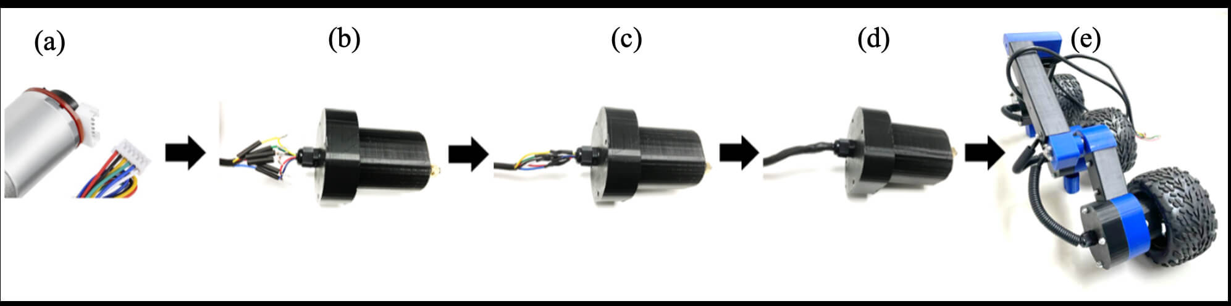
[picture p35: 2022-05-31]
docs/images/MTV/MotAssembly.jpg

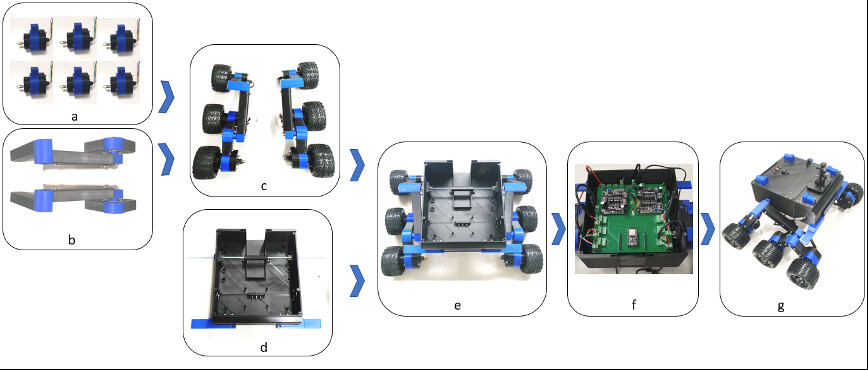
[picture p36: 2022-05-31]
docs/images/MTV/Rover_Assembly.jpg

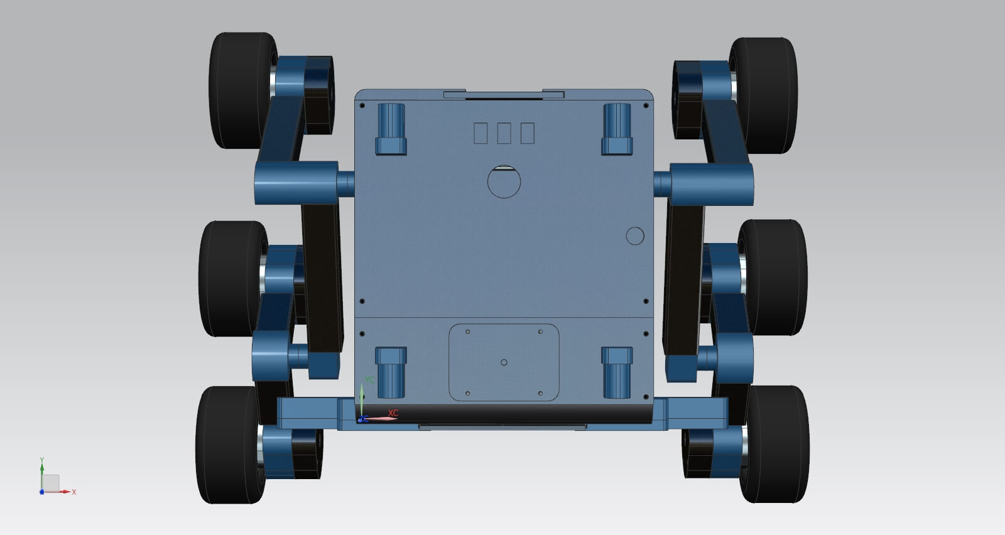
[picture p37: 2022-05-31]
body/mtv/cad/Assembly/3.jpg

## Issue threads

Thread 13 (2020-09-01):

Wiring diagram

Tmin10, 2020-09-01:
May you provide wiring diagram for the robot?

I'm little bit confused with point 17 in the build instructions:
- (Optional) Connect the voltage divider to pin A7 of the Arduino

What is the voltage divider, why we need it and how we can connect it to the robot.

Other question about point 14:
Why we need connect echo and trigger pins together in one arduino port? Other samples told us to use two ports for this...

P.S. Thank you for your project!

thias15, 2020-09-01:
The voltage divider is used to measure the battery voltage. The battery has a voltage of 9.6-12.6V. But the ADC of the Arduino can only measure a voltage of up to 5V. For example, you can use a 20k and 10k resistor and then set the multiplier in the app to 3. One end of the 20k resistor is connected to Vin and the other to the Arduino pin A7 and one end of the 10k resistor. The other end of the 10k resistor is connected to GND. More info [here](https://ohmslawcalculator.com/voltage-divider-calculator).
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

We use the NewPing library for the Ultrasonic sensor. It supports single pin operation and automatically toggles this pin to be an input and output depending if the echo signal is sent or it is waiting for the trigger signal to be received. You can also connect it to two pins as in other tutorials if you prefer. Just make sure to keep it event-driven as in the code, otherwise the ultrasonic sensor will block the rest of the code.

Tmin10, 2020-09-01:
Got it. So voltage divider is about arduino power supply.
Maybe it's better to use some DC-DC convertor since we losing part of the energy as heating on resistors

Tmin10, 2020-09-01:
Hm, I reread instructions again and looks like this voltage divider isn't for power supply, sorry.
Is it for battery charge level checking? I confused because there is no resistors in the bill of materials...

thias15, 2020-09-02:
Yes, it is to check the battery voltage and it is optional.

thias15, 2020-09-04:
Closing due to inactivity.

Tmin10, 2020-09-04:
I'm sorry but my request still open. Maybe in future you can add picture with the wiring diagram?
In other issue I found question about wiring motors. It could help with robot assembly for others.

thias15, 2020-09-04:
I have added a wiring diagram. Does this answer your questions? If not feel free to reopen the issue or open another one.

Tmin10, 2020-09-04:
Cool, thank you! Sorry, I missed your commit.

Closed 2020-09-04.

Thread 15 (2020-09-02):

[Feature] Button to switch camera

Tmin10, 2020-09-02:
Hello. I run the app on my phone but it display picture from front camera. After debugging I realize that I need to change https://github.com/intel-isl/OpenBot/blob/master/android/app/src/main/java/org/openbot/CameraActivity.java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 to 0 (LENS_FACING_FRONT) and it working fine... I don't know why front and back are reversed in my case but it could help you in future for debug the same problems.

My device is Asus Zenfone Max Pro (M2) ZB631KL, Android 9. Other cameras apps working fine.

thias15, 2020-09-02:
We have not encountered this on any phone before. Thanks for opening this issue, we will keep an eye on it. I will close it for now, since I don't expect this to be a general issue.

Tmin10, 2020-09-02:
Yep, thanks. Maybe in future it is possible to add camera switch into the settings.

eagleanurag, 2020-10-11:
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

tin my case also when i used my old Samsung J7 Max by default front camera opens

vkuehn, 2020-11-17:
Hi I have a solution for that, can you kindly assign it to me ?
Sorry it will be not fully compliant with your naming rules..this time

vkuehn, 2020-12-08:
is there an issue why it is a ToDo again ?

Closed 2020-11-19.

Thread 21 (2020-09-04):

Which motors connect to which output?

mikeh9, 2020-09-04:
Really appreciate your project and all the hard work you put in. I know the wiring diagram is coming, but can you comment on which motors goes to Out1/2 and which motors go to Out3/4?

I'm writing this to help others out as well. :-)

thias15, 2020-09-04:
Insert the positive and negative leads of the two **left** motors into OUT1 (+) and OUT2 (-) of the L298N board

Insert the positive and negative leads of the two **right** motors into OUT4 (+) and OUT3 (-) of the L298N board

The reason that +/- is swapped for left and right is that the motors are mounted with 180 degrees rotation, so they turn in the opposite direction.

The leads of the motors on the same side are connected, since they are controlled by the same H-bridge. I recommend to solder the wires of the same polarity for both motors on the same side. This way it's easier to install them and make sure there is a good connection.

moosa1996, 2020-09-04:
Hi I have a issue on connecting my nano USB to my mobile type c. cant able to establish USB Connection.I have enabled my developer USB debugging in my android mobile. But still device is not connected in OpenBot app.What is the issue ?

mikeh9, 2020-09-04:
Your reasoning is correct, but I think you mistyped what you meant. I think you wanted to write:

Insert the positive and negative leads of the two left motors into OUT1 (+) and OUT2 (-) of the L298N board

Insert the negative and positive leads of the two right motors into OUT3 (+) and OUT3 (-) of the L298N board

With this configuration my car runs properly. Now onto the training. :-)

Closed 2020-09-04.

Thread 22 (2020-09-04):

Openbot Android app

moosa1996, 2020-09-04:
Hi I have a issue on connecting my nano USB to my mobile type c. cant able to establish USB Connection.I have enabled my developer USB debugging in my android mobile. But still device is not connected in OpenBot app.What is the issue ?
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

francisduvivier, 2020-09-04:
Which phone do you use? It might not support USB OTG

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

thias15, 2020-09-04:
When you first connect the Arduino to your phone it will ask you for permission to access the USB device. Did you see this dialog?

If **yes**, you need to give permission.

If **no**, you probably have a connection issue.
- Double-check the baud rate of App and Arduino are the same (they should be unless you changed something.
- Try another cable.
- Confirm your phone supports USB-OTG.

mikeh9, 2020-09-04:
Can you confirm you used the cable specified in the BOM? It needs to be an OTG cable (ID connected to ground)

moosa1996, 2020-09-05:
> Which phone do you use? It might not support USB OTG
> […](#)
> On Fri, Sep 4, 2020, 13:01 moosa1996 ***@***.***> wrote: Hi I have a issue on connecting my nano USB to my mobile type c. cant able to establish USB Connection.I have enabled my developer USB debugging in my android mobile. But still device is not connected in OpenBot app.What is the issue ? — You are receiving this because you are subscribed to this thread. Reply to this email directly, view it on GitHub <#22>, or unsubscribe <https://github.com/notifications/unsubscribe-auth/AASZQZ4QTUQXR5QGUUQSVCDSEDCH5ANCNFSM4QYCQNOA> .

moosa1996, 2020-09-05:
> Which phone do you use? It might not support USB OTG
> […](#)
> On Fri, Sep 4, 2020, 13:01 moosa1996 ***@***.***> wrote: Hi I have a issue on connecting my nano USB to my mobile type c. cant able to establish USB Connection.I have enabled my developer USB debugging in my android mobile. But still device is not connected in OpenBot app.What is the issue ? — You are receiving this because you are subscribed to this thread. Reply to this email directly, view it on GitHub <#22>, or unsubscribe <https://github.com/notifications/unsubscribe-auth/AASZQZ4QTUQXR5QGUUQSVCDSEDCH5ANCNFSM4QYCQNOA> .

I'm using One plus 5T which supports OTG

moosa1996, 2020-09-05:
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

Yes it asked for permission to access the USB device. I gave yes and the openbot app opens automatically when my arduino nano is plugged into OTG. but when the app is opened it shows a dialogue text "Please Check the USB Connection". Why so?

moosa1996, 2020-09-05:
> Can you confirm you used the cable specified in the BOM? It needs to be an OTG cable (ID connected to ground)

I used 2 type of cable converter. One is "Type C to USB female" and other is "Mini to USB male" i have attached my converter cables for your reference
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

thias15, 2020-09-05:
Should work in principle, but we never tried with adapters. Can you verify with another phone or device that the cables work?

thias15, 2020-09-07:
What happens when you try to toggle the connection switch in the app? Are you sure the Arduino has the firmware flashed correctly? Can you try to flash it again and then open the serial monitor to see if the Arduino is connecting and sending it's messages.

thias15, 2020-09-09:
Closing due to inactivity.

Closed 2020-09-09.

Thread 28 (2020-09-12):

Vin/ADC7 in schematic

caiograg, 2020-09-12:
Hey, guys, awsome work!

On the wiring diagram, Vcc is connected to the A7 pin in the Arduino Nano, is that correct?

I have a battery pack which I'll use because it is rechargeable. I intended to connect the 5V regulated output from the driver board to the Vin Arduino pin.

Will try and give some feedback on my attempt here!

-Caio

caiograg, 2020-09-12:
Reread the build instructions. My bad! This is used to check the battery. Closing issue.

Closed 2020-09-12.

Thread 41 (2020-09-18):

the slim version doesn't fit on plate 223x223

ronki2304, 2020-09-18:
Hello I tried to print the slim version

but body_top_slim.stl doesn't fit

I used an ultimaker 2 which have a plate of 223*223mm

thias15, 2020-09-18:
Did you rotate it by 45 degrees?

ronki2304, 2020-09-18:
Yes I have rotated it

the bottom filled  perfectely but not the top

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

I see your PR, I don't know what is the difference, but the model doesn't fit on cura

thias15, 2020-09-18:
In the bottom left, the dimensions show as 223x223. Is there maybe some setting in Cura?

thias15, 2020-09-19:
Any luck?

ronki2304, 2020-09-21:
Hello sorry for my late answer,

what do you mean by some settings ???? those dimensions are the piece one on the build plate

thias15, 2020-09-21:
Well, you have an ultimaker 2 which as a build plate of 223x223. The model is also 223x223, so it should fit. So you probably have some setting enabled which prevents you from using the complete build area.

- Have you selected build plate adhesion with a brim or a skirt?
This will increase the overall size of your print.
To disable it, set *Build Plate Adhesion Type* to "None".

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

Other settings that are probably not necessary, but may help to fit the model:
- Disable the second extruder
- Disable prime blob (under build plate adhesion)

ronki2304, 2020-09-21:
Hello,
the build plate adhesion is already set to off and I don't have a second extruder,

i tried to change the g-code flavor but I don't see any change. i don't which setup has been made by @katnoria in [PR#2](https://github.com/intel-isl/OpenBot/issues/2)

thias15, 2020-09-21:
@ronki2304 Please try https://github.com/intel-isl/OpenBot/blob/develop/body/slim_body/slim_body_top.stl from the development branch. If this does not work, checkout the glueable model.

ronki2304, 2020-09-21:
OK it works thank you very much

Closed 2020-09-21.

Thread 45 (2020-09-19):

有了PCB版，和组件的接线是什么样的？

2like, 2020-09-19:
@zhaoyshine
如题，能否补充下中文版readme。

zhaoyshine, 2020-09-19:
抱歉我按选项一来的，选项二这块我不太清楚，选项一走线我选的 杜邦线 母-母、公-母、公-公接头我各准备了十根，应该够用。目前我东西也还在路上，没有开始

2like, 2020-09-19:
等你选项一的好消息！
@zhaoyshine

thias15, 2020-09-20:
Is this issue resolved?

2like, 2020-09-21:
> Is this issue resolved?

Can you give a detailed description of how to use PCB

thias15, 2020-09-21:
- Attach Arduino Nano to the U1 header
- Connect motors to M1-M4
- Connect power source to Vin
- Connect sensors to the appropriate header pins

2like, 2020-10-09:
> 抱歉我按选项一来的，选项二这块我不太清楚，选项一走线我选的 杜邦线 母-母、公-母、公-公接头我各准备了十根，应该够用。目前我东西也还在路上，没有开始

杜邦线怎么买？搞定了吗？

zhaoyshine, 2020-10-10:
早搞定了，杜邦线 母-母、公-母、公-公接头我各准备了十根，淘宝大把随便买。体验下来自动跟随人体识别有点不行，随便一件衣服就识别成人了，不能稳定跟某一个人，目前一直在玩手柄模式

zhaoyshine, 2020-10-10:
这个是我demo版时拍的照片，应该是对的
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

Closed 2020-09-22.

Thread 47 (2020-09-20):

Unable to compile the firmware

Cantfigurethisout, 2020-09-20:
I am new to this kind of thing, I realized that the firmware needed to get to the arduino board however if you read the documentation it mentions nothing.  I downloaded arduino IDE added the board in the board manager and sent the file to the board.  Got lots of errors in the IDE (don't know if it was something I did), tried to get the thing to drive....... nothing.  After multimeter testing terminals realized pins needed to be uncommented in the firmware.........sent it to the board with a large list of errors.  Still not getting any wheel spinning.  Scratching my head as to the issue.  I have bought everything to stick with the build as documented hoping I could have my handheld as build this.

thias15, 2020-09-20:
What error are you getting? You shouldn't need to comment anything.

thias15, 2020-09-20:
Did you install the NewPing library?

thias15, 2020-09-20:
Also let me give a general recommendation for issues in open-source projects.
1) Don't complain, be nice when asking for help. This is an open-source project. Nobody wants to help a complainer.
2) Be specific about your error. Include screenshots, error logs, etc.
3) If you feel things could be done better, improve them and send a pull request.

crearo, 2020-09-20:
+1 for @thias15 's comment. This is actually one of the best documented hardware+software+3D-printing projects I've seen on GitHub!

Apart from writing out what exactly your current setup is, write about your problem specifically.
Additionally, don't expect this project to have a start-from-scratch guide. If you're new, do you research on things you don't understand first.

Cantfigurethisout, 2020-09-20:
Didn't mean to be a complainer, I apologize for sounding that way, just trying to identify an area that was lacking (everything else has been fairly well documented, or at least it is mentioned what needs to be done).

"You shouldn't need to comment anything."  Don't you have to delete some of the hashtag things to make it work?

#if (OPENBOT == DIY)
  #define PIN_PWM1 5
  #define PIN_PWM2 6
  #define PIN_PWM3 9
  #define PIN_PWM4 10
  #define PIN_SPEED_L 2
  #define PIN_SPEED_R 3
  #define PIN_VIN A7
  #define PIN_TRIGGER   4
  #define PIN_ECHO      4
  #define PIN_LED_RL 7
  #define PIN_LED_RR 8
#elif (OPENBOT == PCB)
  #define PIN_PWM1 10
  #define PIN_PWM2 9
  #define PIN_PWM3 5
  #define PIN_PWM4 6
  #define PIN_SPEED_L 2
  #define PIN_SPEED_R 4
  #define PIN_VIN A7
  #define PIN_TRIGGER   3
  #define PIN_ECHO      3
  #define PIN_LED_RL 7
  #define PIN_LED_RR 8
#endif

As far as errors go I got a lot, need to spend more time with it to make sure I am not doing anything dumb.  Not intending to ask for help yet on fixing my setup, like I said noticed an area that was lacking and wanted to point it out.

If I was going to complain I would start with not being able to print on my ender 3 because the dimensions of the car are too big.  My solution for this sucked and I want to re-do it, if that is halfway decent I will post it so others with a smaller print volume can use it as well.

parixit, 2020-09-20:
Those aren't comments.  These are comments:
// ---------------------------------------------------------------------------
// This Arduino sketch accompanies the OpenBot Android application.
//
// The sketch has the following functinonalities:
//  - receive control commands from Android application (USB serial)
//. - produce low-level controls (PWM) for the vehicle
//  - toggle left and right indicator signals
//  - wheel odometry based on optical speed sensors
//  - estimate battery voltage via voltage divider
//  - estimate distance based on sonar sensor
//  - send sensor readings to Android application (USB serial)
//
//  Dependencies (if sonar is required):
//  - NewPing library by Tim Eckel (Install via Tools --> Manage Libraries)
//
// By Matthias Mueller, Intelligent Systems Lab, 2020
// ---------------------------------------------------------------------------

// PIN_PWM1,PIN_PWM2,PIN_PWM3,PIN_PWM4      Low-level control of left DC motors via PWM
// PIN_SPEED_L, PIN_SPEED_R                  Measure left and right wheel speed
// PIN_VIN                                  Measure battery voltage via voltage divider
// PIN_TRIGGER                              Arduino pin tied to trigger pin on ultrasonic sensor.
// PIN_ECHO                                 Arduino pin tied to echo pin on ultrasonic sensor.
// MAX_DISTANCE                             Maximum distance we want to ping for (in centimeters).
// PIN_LED_RL, PIN_LED_RR                   Toggle left and right rear LEDs (indicator signals)

//------------------------------------------------------//
//DEFINITIONS
//------------------------------------------------------//

thias15, 2020-09-20:
@Cantfigurethisout What you posted are the pin definitions. You just need to set if you are using the DIY or the PCB version. That's all.

If you are building the robot using the DIY instructions just leave as it is:
```
// Setup the OpenBot version
#define OPENBOT DIY
```

If you are using the PCB then change it to:
```
#define OPENBOT PCB
```

What is the size of the build plate on your 3D printer?

thias15, 2020-09-20:
@Cantfigurethisout I just merged a PR that adds a flag to disable the sonar. Try setting `HAS_SONAR 0`. This will remove compile errors related to not installing the NewPing library.

thias15, 2020-09-21:
@Cantfigurethisout any updates?

By the way check out the new [slim model](https://github.com/intel-isl/OpenBot/blob/master/body/cad/slim_body). Top and bottom both fit on a 220mmx220mm build plate. If this is still too big, check out the [glueable model](https://github.com/intel-isl/OpenBot/blob/master/body/cad/glue_body).

Cantfigurethisout, 2020-09-21:
Haven't gotten back to this.  I saw the slim model, however my build volume is 200x200 (I hear this can be increased with open source firmware on my printer however I haven't gotten to that yet).  Didn't see the glueable model, I will look for that. Thanks

Cantfigurethisout, 2020-09-22:
Ok, I tried again, enabled Verbose logging so if this is too much, I apologize.  Copied error code:

Arduino: 1.8.13 (Windows 10), Board: "Arduino NANO 33 IoT"

C:\Program Files (x86)\Arduino\arduino-builder -dump-prefs -logger=machine -hardware C:\Program Files (x86)\Arduino\hardware -hardware C:\Users\jresp\AppData\Local\Arduino15\packages -tools C:\Program Files (x86)\Arduino\tools-builder -tools C:\Program Files (x86)\Arduino\hardware\tools\avr -tools C:\Users\jresp\AppData\Local\Arduino15\packages -built-in-libraries C:\Program Files (x86)\Arduino\libraries -libraries C:\Users\jresp\OneDrive\Documents\Arduino\libraries -fqbn=arduino:samd:nano_33_iot -vid-pid=2341_8057 -ide-version=10813 -build-path C:\Users\jresp\AppData\Local\Temp\arduino_build_869510 -warnings=none -build-cache C:\Users\jresp\AppData\Local\Temp\arduino_cache_836998 -prefs=build.warn_data_percentage=75 -prefs=runtime.tools.arduinoOTA.path=C:\Users\jresp\AppData\Local\Arduino15\packages\arduino\tools\arduinoOTA\1.2.1 -prefs=runtime.tools.arduinoOTA-1.2.1.path=C:\Users\jresp\AppData\Local\Arduino15\packages\arduino\tools\arduinoOTA\1.2.1 -prefs=runtime.tools.arm-none-eabi-gcc.path=C:\Users\jresp\AppData\Local\Arduino15\packages\arduino\tools\arm-none-eabi-gcc\7-2017q4 -prefs=runtime.tools.arm-none-eabi-gcc-7-2017q4.path=C:\Users\jresp\AppData\Local\Arduino15\packages\arduino\tools\arm-none-eabi-gcc\7-2017q4 -prefs=runtime.tools.bossac.path=C:\Users\jresp\AppData\Local\Arduino15\packages\arduino\tools\bossac\1.7.0-arduino3 -prefs=runtime.tools.bossac-1.7.0-arduino3.path=C:\Users\jresp\AppData\Local\Arduino15\packages\arduino\tools\bossac\1.7.0-arduino3 -prefs=runtime.tools.CMSIS.path=C:\Users\jresp\AppData\Local\Arduino15\packages\arduino\tools\CMSIS\4.5.0 -prefs=runtime.tools.CMSIS-4.5.0.path=C:\Users\jresp\AppData\Local\Arduino15\packages\arduino\tools\CMSIS\4.5.0 -prefs=runtime.tools.CMSIS-Atmel.path=C:\Users\jresp\AppData\Local\Arduino15\packages\arduino\tools\CMSIS-Atmel\1.2.0 -prefs=runtime.tools.CMSIS-Atmel-1.2.0.path=C:\Users\jresp\AppData\Local\Arduino15\packages\arduino\tools\CMSIS-Atmel\1.2.0 -prefs=runtime.tools.openocd.path=C:\Users\jresp\AppData\Local\Arduino15\packages\arduino\tools\openocd\0.10.0-arduino7 -prefs=runtime.tools.openocd-0.10.0-arduino7.path=C:\Users\jresp\AppData\Local\Arduino15\packages\arduino\tools\openocd\0.10.0-arduino7 -verbose C:\Users\jresp\Downloads\OpenBot-master\firmware\openbot_v1_nano\openbot_v1_nano.ino

C:\Program Files (x86)\Arduino\arduino-builder -compile -logger=machine -hardware C:\Program Files (x86)\Arduino\hardware -hardware C:\Users\jresp\AppData\Local\Arduino15\packages -tools C:\Program Files (x86)\Arduino\tools-builder -tools C:\Program Files (x86)\Arduino\hardware\tools\avr -tools C:\Users\jresp\AppData\Local\Arduino15\packages -built-in-libraries C:\Program Files (x86)\Arduino\libraries -libraries C:\Users\jresp\OneDrive\Documents\Arduino\libraries -fqbn=arduino:samd:nano_33_iot -vid-pid=2341_8057 -ide-version=10813 -build-path C:\Users\jresp\AppData\Local\Temp\arduino_build_869510 -warnings=none -build-cache C:\Users\jresp\AppData\Local\Temp\arduino_cache_836998 -prefs=build.warn_data_percentage=75 -prefs=runtime.tools.arduinoOTA.path=C:\Users\jresp\AppData\Local\Arduino15\packages\arduino\tools\arduinoOTA\1.2.1 -prefs=runtime.tools.arduinoOTA-1.2.1.path=C:\Users\jresp\AppData\Local\Arduino15\packages\arduino\tools\arduinoOTA\1.2.1 -prefs=runtime.tools.arm-none-eabi-gcc.path=C:\Users\jresp\AppData\Local\Arduino15\packages\arduino\tools\arm-none-eabi-gcc\7-2017q4 -prefs=runtime.tools.arm-none-eabi-gcc-7-2017q4.path=C:\Users\jresp\AppData\Local\Arduino15\packages\arduino\tools\arm-none-eabi-gcc\7-2017q4 -prefs=runtime.tools.bossac.path=C:\Users\jresp\AppData\Local\Arduino15\packages\arduino\tools\bossac\1.7.0-arduino3 -prefs=runtime.tools.bossac-1.7.0-arduino3.path=C:\Users\jresp\AppData\Local\Arduino15\packages\arduino\tools\bossac\1.7.0-arduino3 -prefs=runtime.tools.CMSIS.path=C:\Users\jresp\AppData\Local\Arduino15\packages\arduino\tools\CMSIS\4.5.0 -prefs=runtime.tools.CMSIS-4.5.0.path=C:\Users\jresp\AppData\Local\Arduino15\packages\arduino\tools\CMSIS\4.5.0 -prefs=runtime.tools.CMSIS-Atmel.path=C:\Users\jresp\AppData\Local\Arduino15\packages\arduino\tools\CMSIS-Atmel\1.2.0 -prefs=runtime.tools.CMSIS-Atmel-1.2.0.path=C:\Users\jresp\AppData\Local\Arduino15\packages\arduino\tools\CMSIS-Atmel\1.2.0 -prefs=runtime.tools.openocd.path=C:\Users\jresp\AppData\Local\Arduino15\packages\arduino\tools\openocd\0.10.0-arduino7 -prefs=runtime.tools.openocd-0.10.0-arduino7.path=C:\Users\jresp\AppData\Local\Arduino15\packages\arduino\tools\openocd\0.10.0-arduino7 -verbose C:\Users\jresp\Downloads\OpenBot-master\firmware\openbot_v1_nano\openbot_v1_nano.ino

Using board 'nano_33_iot' from platform in folder: C:\Users\jresp\AppData\Local\Arduino15\packages\arduino\hardware\samd\1.8.8

Using core 'arduino' from platform in folder: C:\Users\jresp\AppData\Local\Arduino15\packages\arduino\hardware\samd\1.8.8

Detecting libraries used...
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
thias15, 2020-09-22:
Did you try to disable the sonar, by setting `HAS_SONAR = 0`

Cantfigurethisout, 2020-09-22:
I have a sonar so wanted to keep it.  will try to disable it and see how that works

Cantfigurethisout, 2020-09-22:
It worked, got the wheels spinning.  Thanks for the help.

Closed 2020-09-22.

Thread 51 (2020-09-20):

Can't get the motors working with app control

parixit, 2020-09-20:
Basic setup but can't get the motors running with app control.  Any help is appreciated!

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

[https://youtu.be/muJt_BANYZw](url)

thias15, 2020-09-20:
1) Are the pins D5/D6 and D9/D10 connected to the L298N and are the jumpers to enable PWM in place?

2) Does the LED light blink every time you move the joystick? This indicates the message is sent to the Arduino. If not try reconnecting the USB and verify the baud rate.

3) Can you try to pull the code and recompile the Android app. Early on there was a bug which would skip some intermediate control signals due to some type conversion.

thias15, 2020-09-21:
I assume your issue is solved by (3). Please update the issue after pulling the latest code from the repo and testing.

parixit, 2020-09-21:
Hello @thias15 just did a new pull and build of the app and still the same issue.  I created a video of the issue: [https://www.youtube.com/watch?v=muJt_BANYZw&feature=youtu.be](url)

parixit, 2020-09-21:
Are the pins D5/D6 and D9/D10 connected to the L298N and are the jumpers to enable PWM in place?
**Yes**

Does the LED light blink every time you move the joystick? This indicates the message is sent to the Arduino. If not try reconnecting the USB and verify the baud rate.
**Yes, the LED light blinks every time I move the joystick**

BrandenSebring, 2020-09-21:
@parixit the issue may be in the phone itself. We have found that older phones (such as the note 4) did not send the "bluetooth information correctly" from the controller to the phone then out via usb otg serial to the board. When we changed the phone to a more powerful note 8 everything worked correctly, as far as controller support and motors actually moving.

learning the AI part now, with collected data

Also in the application when using the controller we keep drive mode on "game" and processing on the cpu. other wise the controller acts funny... (using 8bitdo contoller they made for nintendo switch)

and @thias15 thank you and all involved so much for this project!!!

thias15, 2020-09-21:
@BrandenSebring good point. The oldest phone we have tested was about 3 years old. @parixit what phone are you using? One thing you could try is to echo the control sent to the Arduino back to the phone and log it.

Here is a quick and dirty way to do it.

In the Arduino code replace lines 316-328:
```
void sendVehicleData()
{
  Serial.print(getVoltage());
  Serial.print(",");
  Serial.print(counter_left);
  Serial.print(",");
  Serial.print(counter_right);
  Serial.print(",");
  Serial.print(distance_cm);
  Serial.println();
  counter_left = 0;
  counter_right = 0;
}
```

with

```
void sendVehicleData()
{
  Serial.print(getVoltage());
  Serial.print(",");
  Serial.print(ctrl_left);
  Serial.print(",");
  Serial.print(ctrl_right);
  Serial.print(",");
  Serial.print(distance_cm);
  Serial.println();
  counter_left = 0;
  counter_right = 0;
}
```

replace lines 181-183:
```
    if (ctrl_rx) {
      processCtrlMsg(inChar);
    }
```

with
```
    if (ctrl_rx) {
      processCtrlMsg(inChar);
      sendVehicleData();
    }
```

Now connect everything and press the X button on the controller. The phone will start logging (you will hear the voice feedback "start logging"). Then move the joysticks to generate control signals (in game mode the trigger is used for throttle and joystick for steering). After some time stop the logging by pressing the X button again. Now, go to the log folder and look at the vehicle log file. In place of the speed sensor readings you will now see the control signals that were received. Can you post this here?

parixit, 2020-09-21:
@thias15 I am using a LG Rebel 4 (L212VL) which was released in 2018.  More info on the phone: https://www.phonemore.com/specs/lg/rebel-4/

I am using a PS4 controller and I hit the Square button to start testing.  The X button on the controller doesn't do anything for me.

What's weird is I don't see new zip files created for my test today.  Anything I have to do in the app?
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

thias15, 2020-09-21:
Logging was working before but not anymore? Logging should be triggered by the X button on the PS4 controller. The circle and square buttons control the indicators.

Do you hear "logging started" and then "logging stopped"?
You don't need to do anything besides starting the log and the stopping it which will zip all the data. If the buttons are not working properly, you can also toggle logging the the app.

parixit, 2020-09-21:
Yes, I do hear logging started and logging stopped.  But I hit the Square button on my PS4 controller to start logging.  The X button does not trigger logging.  It looks like logging was working before but now I don't see new files in OpenBot folder.

thias15, 2020-09-21:
The phone is on the lower end and only supports Android 7/8. We have tested the Nokia 2.2 which has similar performance as your phone but has Android 9. It worked, but was not able to run the AI models perfectly. You may have a hard time running the AI models at a decent speed as well. Do you have access to another phone?

thias15, 2020-09-21:
Hm. It seems like there is an issue with the button mapping. How about if you toggle logging in the app. Does that work?

parixit, 2020-09-21:
I am an iPhone user and this is a burner phone I use to test.  Not sure if I want to buy a high end Android phone for this as it defeats the purpose of a low cost bot.

parixit, 2020-09-21:
What is weird is when I manually toggle logging in the app (not with a controller) it doesn't say "Logging started", "Logging stopped".  It does say it when I press the square button on the PS4 controller.

thias15, 2020-09-21:
Yes, makes sense. Not saying you should buy a new phone, but maybe some in the family has one to try.

thias15, 2020-09-21:
One thing you could do is to print the joystick commands received inside the GameController class. Then you keep the phone connected to the laptop and look at the debug output.

thias15, 2020-09-21:
When you use the button in the app there is no audible feedback. It is just meant for operation via game controller when the screen is not visible.

parixit, 2020-09-21:
> One thing you could do is to print the joystick commands received inside the GameController class. Then you keep the phone connected to the laptop and look at the debug output.

Can you walk me through this?  I see GameController.java in Android Studio.

thias15, 2020-09-21:
Are you already on the Slack channel?

thias15, 2020-09-21:
Actually, even easier. Just add `gameController.processButtonInput(event);` at the top of the function `public boolean dispatchKeyEvent (KeyEvent event)` in NetworkActivity.java.

thias15, 2020-09-21:
You should then see toast messages in the app when you press different button. What message shows up when you press the "X" button or the other buttons?

parixit, 2020-09-21:
No not in the slack channel, do you need to add me?  If so please do add me.
So, like this?
public boolean dispatchKeyEvent (KeyEvent event) {
    // Check that the event came from a game controller
    gameController.processButtonInput(event);

thias15, 2020-09-21:
Yes.

thias15, 2020-09-21:
For checking what controls are being sent out, add the LOGGER to line 985 in CameraActivity.java
```
  protected void sendControlToVehicle(ControlSignal vehicleControl) {
    if ((usbConnection != null) && usbConnection.isOpen() && !usbConnection.isBusy()) {
      String message = String.format("c%d,%d\n",
              (int) (vehicleControl.getLeft() * speedMultiplier),
              (int) (vehicleControl.getRight() * speedMultiplier));
      **LOGGER.d("Control: " + message);**
      usbConnection.send(message);
    }
  }
```

parixit, 2020-09-21:
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

That broke:
OpenBot/android/app/src/main/java/org/openbot/CameraActivity.java:990: error: illegal start of expression
      **LOGGER.d("Control: " + message);**

` protected void sendControlToVehicle(ControlSignal vehicleControl) {
    if ((usbConnection != null) && usbConnection.isOpen() && !usbConnection.isBusy()) {
      String message = String.format("c%d,%d\n",
              (int) (vehicleControl.getLeft() * speedMultiplier),
              (int) (vehicleControl.getRight() * speedMultiplier));
      **LOGGER.d("Control: " + message);**
      usbConnection.send(message);
    }
  }`

thias15, 2020-09-21:
Then compile and run app. Keep it connected to USB of the laptop and connect the BT controller. Select *6:Logcat* from the bottom, and enter "Control:" in the search window. Now when you move joysticks on the game controller, you should see the messages being sent in the Window. Can you post them here?

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

thias15, 2020-09-21:
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

My bad, remove the ** around LOGGER, was trying to make it bold, but forgot I'm in code mode...
`LOGGER.d("Control: " + message);`

thias15, 2020-09-21:
> Are you already on the Slack channel?

Join [Slack](https://join.slack.com/t/openbot-community/shared_invite/zt-hpso8cfl-JO9OVhVMdUWvR4vDXwcMGA)

parixit, 2020-09-21:
A/libc: Fatal signal 11 (SIGSEGV), code 1, fault addr 0x8c080000 in tid 15642 (org.openbot), pid 15642 (org.openbot)
Changes were not applied.
We were unable to deploy your changes: MISSING_AGENT_RESPONSES

thias15, 2020-09-21:
Can you restart Android studio and try again?

parixit, 2020-09-21:
Ok, an update on where we are.  Big thank you to @thias15 for walking me through.
Turned on logging and for some strange reason my PS4 controller is triggering logging with the square button instead of the X.  Will try to another usb cable and to try to send a signal from the Arduino to the pins directly.

BrandenSebring, 2020-09-21:
@parixit when we used the older phone(note 4) , it would log start and stop with different button (we heard it) and the "blinkers" would get hit with gas or r1 buttons. This sounds like something in android is mapping the buttons differently.

parixit, 2020-09-23:
I finally got the motors to move!  It turns out I had a bad L298N board.  I am pasting firmware code for the Arduino Nano to test the motors.  If others are having the same issue this helped me troubleshoot.
`//This is to test the motors
//It will send a signal to move the motors

  //set up pins
  #define PIN_PWM1 5
  #define PIN_PWM2 6
  #define PIN_PWM3 9
  #define PIN_PWM4 10

void setup() {
  // put your setup code here, to run once:

  //Outputs
  pinMode(PIN_PWM1,OUTPUT);
  pinMode(PIN_PWM2,OUTPUT);
  pinMode(PIN_PWM3,OUTPUT);
  pinMode(PIN_PWM4,OUTPUT);

}

void loop() {
  // put your main code here, to run repeatedly:
  analogWrite(PIN_PWM1, 128);
    analogWrite(PIN_PWM2, 0);
    analogWrite(PIN_PWM3, 128);
    analogWrite(PIN_PWM4, 0);
    delay(5000);

}`

Closed 2020-09-23.

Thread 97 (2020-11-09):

The 3D printing file size is not suitable for the I3 frame printer, ha ha!

38293312, 2020-11-09:
I really like this project and want to DIY one, but my I3 frame 3D printer cannot print OPEBOT files. I have a headache!
I just read the related articles and found that the "speed sensor" has no model. I found it on the Internet and there is no one. Can you tell me an alternative model? Can all modules of this signal be used?
"The slot-shaped through-beam photoelectric, as long as the non-transparent object passes through the slot, it can trigger to output 5V TTL level. Using Schmitt trigger to de-jitter pulse"

thias15, 2020-11-09:
Could you please elaborate why you cannot print?

I assume the speed sensor is an unrelated issue. What do you mean by model of the speed sensor? It is an optical encoder and the disk attached to the motor shaft, interrupts the optical signal. By counting the interrupts, the number of rotations can be measured.

38293312, 2020-11-09:
> 您能否详细说明为什么无法打印？
>
> 我认为速度传感器是一个无关紧要的问题。速度传感器的型号是什么意思？它是一个光学编码器，并且光盘固定在电机轴上，可中断光学信号。通过计算中断次数，可以测量转数。

Hahaha, what I mean by unprintable means that the size of the object exceeds the size that the I3 printer can print.
Can the speed sensor not be used?

thias15, 2020-11-09:
You can try the [glueable body](https://github.com/intel-isl/OpenBot/tree/master/body/cad/glue_body). As for the speed sensor, yes it should work. Are you asking about a specific model that's different from the one in the BOM?

38293312, 2020-11-10:
> 您可以尝试可[胶粘的身体](https://github.com/intel-isl/OpenBot/tree/master/body/cad/glue_body)。至于速度传感器，是的，它应该可以工作。您是否要询问与BOM表中的模型不同的特定模型？

Yes, after your reminder, I noticed that there are close-up models in the BOM! Thank you very much, so you can print, I am preparing electronic components, ready to assemble one by hand, thank you again for sharing!

Closed 2020-11-11.

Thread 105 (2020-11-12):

Issue with Indicator Log?

zlite, 2020-11-12:
The Jupyter Notebook doesn't like the IndicatorLog.txt file

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

thias15, 2020-11-13:
Check if the indicatorLog is empty. If there is only the header, you can add `0,0` in the next line. It should add the status of the indicators at the beginning of the log automatically to make sure it's never empty. I will look into this issue. As workaround, you can press the triangle button on the PS4 at the start of the recording, or manually add an entry as described above.

zlite, 2020-11-13:
Yes, that was the problem. One of the indicatorLogs in one of the runs had only the header. I added 0,0 and it now trains

thias15, 2020-11-13:
Great to hear it. I will double-check the Android code and see if I can reproduce and fix this issue.

zlite, 2020-11-13:
I'm now getting errors again, despite checking that all the IndicatorLog.txt entries had a header and at least one entry. Very frustrating.
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

My datasets are [here](https://drive.google.com/drive/folders/14VfBgP-RqKDuHjsf0Dv8rGd025HkR6cn?usp=sharing). Can you see anything obviously wrong with them?

thias15, 2020-11-14:
Some of you ctrl_log files in both train_data and test_data are completely empty. I will revisit the code the make it more robust and produce more meaningful error messages. But I'm not sure how you ended up with empty files. I have collected several hours of data, and not encountered such issues. If you can figure out why you have these empty files, please let me know so I can fix it.

zlite, 2020-11-14:
Wow -- I've got no idea! The only change I made to the Android app was the one you suggested to not display the long Chinese Arduino board name.

I presume the ctrlLog.txt is tracking my PS4 controller input? But I notice that there are a lot of other zero-length sensor files in some of those runs, too.

I'm not quite sure how to properly exit the Android app when I'm done, so after I press X to stop logging, I just disconnect the phone from the bot and sometimes after that the app freezes. Do you think that a bad exit from the app could cause those zero-length files?

zlite, 2020-11-14:
One other possibility. I changed the Arduino code to use quadrature encoders, and I wonder if the interrupts are disrupting some serial flow at 115k. I also get freezes after a few minutes of driving, like this report:
https://openbot-community.slack.com/archives/C01BRGE07QQ/p1603981059143500

My modified Arduino code is [here](https://github.com/zlite/OpenBot/blob/master/firmware/openbot_new.ino)

Maybe I should be logging at a slower serial rate, like 57k?  It's been a long time since I used classic Atmega 328 Arduinos (as opposed to modern boards, like Teensy or 32u4) so maybe they can't handle 115k serial and interrupts at the same time?

thias15, 2020-11-14:
The best way to exist the app is via the back button. Make sure to wait a little bit after collecting the data before you kill the app, to make sure the data is completely written.

>I presume the ctrlLog.txt is tracking my PS4 controller input?

Yes.

>But I notice that there are a lot of other zero-length sensor files in some of those runs, too.

Yes, if the sensors don't exist on your phone some files will be empty. But only the control and indicator logs are currently used.

zlite, 2020-11-14:
Interestingly, on the runs where the ctrlLog size is zero, most of the other sensors are also zero, even though my phone has those sensors and other runs they're not zero. So it definitely looks like a logging issue with the Android app;

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

thias15, 2020-11-15:
Is it possible that the app crashed or was killed in these instances? Because if the log is not closed properly, it may be empty. The file does not get saved after each timestep, but only after the buffer is full or after logging is stopped.

thias15, 2020-11-18:
With further testing I was not able to reproduce. Will close it for now. Please reopen if you have any idea what caused the issue in the logs so I can fix it.

Closed 2020-11-18.

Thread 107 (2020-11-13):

Cannot test with "c128,128" command!

38293312, 2020-11-13:
After successfully encoding with the latest code, the OLED display is normal. I just made the most basic connection. Now I mainly test whether the 4 motors are normal. Using "Cannot test with "c128,128" command", the motor does not rotate, the serial port software The card does not change on line 10.

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

38293312, 2020-11-13:
I tried both the high and low OE driven by the L298N motor, but it still couldn't rotate.

thias15, 2020-11-13:
It looks like your Arduino is not connected to GND. You need to wire the GND pin from your Arduino to the GND of the L298N.

thias15, 2020-11-13:
Another thing you can check is if the new line terminator is enabled in the serial monitor. By default it should be.

38293312, 2020-11-13:
> 您可以检查的另一件事是在串行监视器中是否启用了新的线路终止器。默认情况下应该是。

The GND and arduino GND of the L298N 12V power supply are connected together, and the test with a multimeter is OK

38293312, 2020-11-13:
thank you very much. The problem is solved!

thias15, 2020-11-13:
How did you solve the problem in the end?

Closed 2020-11-13.

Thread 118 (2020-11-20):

How to charge my phone right on the robot ?

quockhanh1198, 2020-11-20:
Hi Thias, when I run the model with the phone's GPU the performance is very good so I intend to set it up by default, but the phone is quite battery consuming and I am not sure how to maintain the battery of the phone by charging the phone on robot most effective. Can you help me? Thank you so much !

thias15, 2020-11-20:
You could try a cable like [this](https://www.amazon.com/dp/B07CG3MR48). Connect one end to the Arduino and another to a power bank. Another option, if you are good with electronics/soldering is to open a USB cable and connect the 5V lines to the regulator on the L298N.

quockhanh1198, 2020-11-20:
Thank you for your reply

JamesNewton, 2021-03-12:
Many phones will not charge and operate an OTG device at the same time. I made a list of the ones that do. Also of some tablets and phones which have a seperate power jack.
http://www.massmind.org/techref/io/usb/otg.htm

Closed 2020-11-23.

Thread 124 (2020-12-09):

[Feature] Maintain settings on configuration changes and between app runs

msesma, 2020-12-09:
Current implementation of the app maintains the camera selection on configuration changes, like a device rotation.

This feature proposal if for maintaining all settings not only during configuration changes but also between app runs.

Settings that will be persisted:

- Data Logger, and logging state.
- USB connection speed.
- Drive mode
- Camera
- Vehicle control
- Model
- Device
- Threads

Settings that won't be persisted

- Controller switch (For safety reasons)
- Connection switch (It changes automatically if a device is connected)

thias15, 2020-12-09:
This sounds great! I think the logging state should probably not be persistent either, since logging is usually turned on/off by a user during data collection. Thanks @msesma.

msesma, 2020-12-09:
Sounds reasonable. In that case I´ll make logging state survive configuration changes only.

vkuehn, 2020-12-10:
@msesma there is already some psersistence for the camera switch. please make sure it doesn't conflict with your changes

msesma, 2020-12-10:
@thias15 there is no need to persist camera on configuration changes anymore as it is persisted even between runs. But I will use that to persist log mode instead.

Closed 2020-12-11.

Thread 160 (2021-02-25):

Gerber files request

xebbmw, 2021-02-25:
Hello,

I found this interesting project and I would like to build it as an educational project.

I am planning to submit the Gerber files to a manufacturer and then solder the parts myself using a hot air station and a solder iron.

Soldering 0603 SMD parts is doable, but I would prefer instead to solder 0805 SMD. Please provide another version of Gerber files (v2a) where the parts in size 0603 are replaced by 0805 size.

Thanks in advance for your help.

thias15, 2021-02-25:
The gerber files are in the repo. Please refer to the [README](https://github.com/intel-isl/OpenBot/tree/master/body/pcb/README.md) for more info.

xebbmw, 2021-02-25:
> If you prefer I can give you access to the EasyEDA project or export it to a format you can work with. Then you can make any required changes yourself.
Hello,
Thanks for your help. I would prefer access to the files in Eagle CAD (version 7.50) or KiCAD format. Then I can do the required changes myself. Later I can provide you the new version, maybe others would be interested too.

thias15, 2021-02-25:
That sounds great. Here is the converted file (in KiCAD format). There were a few warnings during the conversion. So please let me know if the attached file works. [
[PCB_OpenBotV2.kicad_pcb.txt](https://github.com/intel-isl/OpenBot/files/6045532/PCB_OpenBotV2.kicad_pcb.txt)
](url)

xebbmw, 2021-02-26:
Thanks, I tried to open the file. Not sure if it is the correct file, because I see the PCB has different components (about 13 resistors, 4 capacitors and an small integrated circuit with 48 pins) and also a different layout. See attached file how it looks in Kicad:
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
Also there is another problem, in Kicad I only see pads not the component itself (like resistor for example). It will be difficult in this way to change the component footprint size just by manipulating the pads size.

thias15, 2021-03-02:
Sorry, it seems I uploaded the wrong file by mistake. I have reuploaded. The problem is that I can only export a json file from EasyEDA. I found an online tool to convert to kicad, but it is possible that the components are lost in that process. Here is also the original [json file](https://github.com/intel-isl/OpenBot/files/6071067/DRV8871_Rev2_2021-03-02_19-55-05.json.txt). This is the tool I used [easyeda2kicad](https://wokwi.com/easyeda2kicad). Hope this helps. I have reopened the issue. If this still not works, I can make the changes and provide an updated Gerber file.

xebbmw, 2021-03-03:
Thanks a lot, this time worked just fine! I was able to convert the file and then open it in Kicad. I made the changes for the components C1, C2, LED1, R7, R1, R2, these are now in 0805 format. Here is how it looks right now:
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
I will enlarge just a bit the tracks and then I will generate the Gerber file. I will provide you the files afterwards.

thias15, 2021-03-03:
Thanks @xebbmw. The only thing is that the OpenBot logo and text seem to be messed up by the conversion. But I guess that is not a big deal.

xebbmw, 2021-03-04:
I added the logo that I found on Github, but I could not find the second logo that is in the middle of the board. Also I don't know if there is something else on the other side of the board.
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
Please add the second logo so I could insert it also.

thias15, 2021-03-04:
Not sure how to export the icon. You could just find one with a permissive license that looks similar. The icon is just to show the the PCB may become hot during operation and should not be touched. There is nothing on the other side of the board for now.

xebbmw, 2021-03-06:
I added the second logo from the file pcb_2d_v2.png from this repository and then I imported it. This is the new version with a screenshot from the Gerber viewer.
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
If is ok with you, I will send you all the Gerber files so you can add them to the repository.

thias15, 2021-03-08:
Yes, that would be great. Thanks a lot! This will be very helpful for ppl who want to solder by hand.

xebbmw, 2021-03-12:
I attached a zip file with all the Gerber files. Thanks once again for providing me the sources!
[gerber_v2a.zip](https://github.com/intel-isl/OpenBot/files/6127380/gerber_v2a.zip)

Closed 2021-03-08.

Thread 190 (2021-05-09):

Can't see Video on PC (Windows 10) with python

bender2po, 2021-05-09:
**Describe the bug**
Can't see Video on PC (Windows 10) with python.

**To Reproduce**
Steps to reproduce the behavior:
1. Go to 'cmd'
2. Type  'python keyboard-pygame.py --video'
3. See error: I cannot see any video stream of the robot.

**Expected behavior**
I am expecting to see a video pop-up and which displays camera-view of the robot.

**Screenshots**
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

**Desktop (please complete the following information):**
 - OS: Windows 10

**Smartphone (please complete the following information):**
 - Device: Motorola 5gs plus

thias15, 2021-05-09:
It's not tested on Windows but should work. On the phone are you on the FreeRoam screen? Only on that screen video is implented right now. Does the connection work otherwise, i.e. can you control the bot with the keyboard?

bender2po, 2021-05-09:
Thank you for the response.

I checked for 'Default' and 'FreeRoam' screens. Video stream is not working for both.

I think connection is established because I can see speed and steering values changing on the FreeRoam-screen on the phone, according to the keyboard input.

Currently, I am performing only open-loop testing, i.e., the bot is not connected yet.

thias15, 2021-05-09:
Ok, video should also work open loop. Just the latency is currently still a bit too high to drive. Have you agreed to the permissions for camera and audio? @izivkov do you have any idea what the problem might be?

izivkov, 2021-05-09:
From the screenshot, looks like the python app is disconnected at this time. The last line reads "Received"only, which means the program did not receive any data from the Bot, and this causes the python program to exit. Try restarting the python and establish connection again.
If no video, try switching between FreeRoam and Default screen, a few times. In FreeRaom screen, should see video.

bender2po, 2021-05-10:
I don't think connection disconnected because I can still control the values (speed, steering on FreeRoam) via keyboard.

I tried as @izivkov suggested. Still no luck. Please see screen-shot below:
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

izivkov, 2021-05-10:
Hmm, there should be "VIDEO_SERVER_URL" and "VIDEO_COMMAND" sent to the python program, which I don't see. Did you press the "Controller" button (left most button at the bottom of the FreeRoam screen on the android app)? This should change its icon from a controller to a phone.

izivkov, 2021-05-10:
I can see two reasons why the video is not started:
1. Camera permissions is not set. You can manually check this by going to the app settings, find the OpenBot app, and check permissions. If not set, you can set the camera permission manually from there.
2. The network connection is of type "Nearby", which cannot carry video. This happens if WiFi on the phone is turned off, or you are not logged in to a WiFi network. Make sure both the Phone and the PC are connected on the same WiFi network. As I mention in response to another issue, the Hotspot should not be one of the devices. Please try another hotspot, like another phone, and both the Bot phone and the PC should connect to this hotspot.

izivkov, 2021-05-10:
You also updated to the latest app version, right? The python script works with the latest APK.

bender2po, 2021-05-10:
I am also expecting to see "VIDEO_SERVER_URL" and "VIDEO_COMMAND" in order to satisfy the python's 'if-conditions'.

1. Camera, Location, Microphone, Storage permissions were given.
2. I tried connecting Computer (python) and Phone (OpenBot) to the router as well as another phone's hot spot. Same result in the both scenarios. That is video is not working. However, I could play with keyboard on computer, and, see speedometer and steering GUI on OpenBot app is changing nicely (ie, no visual delay).
3. I am using 'OpenBot-0.3.1.apk'. Is this the latest one?

izivkov, 2021-05-10:
OK, forget what I said about the network connection type. I deleted this comment. This is not the problem since you are communicating to the python script.
So, just check the following:
1. You are running the latest APK for the bot app.
2. Your camera permission is enables in the setting for the OpenBot app.
3. You are using  a third device for hotspot.

izivkov, 2021-05-10:
You can download the app from here, using the barcode:

https://github.com/intel-isl/OpenBot/tree/master/android

bender2po, 2021-05-10:
The barcode directs me to the version 'OpenBot-0.3.1.apk'. Which is already in use.

izivkov, 2021-05-10:
Yes, I need to investigate a bit more. All the basics are correct and it should work. Maybe you can help by trying with a different phone.

bender2po, 2021-05-10:
I just tried with Oneplus-Nord. Still no luck.

thias15, 2021-05-10:
Can you try the latest OpenBot app version from master? You can download it from [here](https://github.com/intel-isl/OpenBot/actions/runs/818493537).

bender2po, 2021-05-10:
@thias15 It is getting stuck here:
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

thias15, 2021-05-10:
Ok, you are almost there now. In principle you should then  see a window with the video stream open. It may take a few seconds. Does it just get stuck there indefinitely? Did you move/rotate the phone in the meantime? This can cause issues since on every rotation it will try to reconnect.

bender2po, 2021-05-10:
Yes, it is stuck indefinitely!!

I locked the phone screen in Potrait in one scenario and Landscape in an another scenario. In both the scenarios the python-script got stuck. (FYI, the phone getting heated up nicely. I guess the phone is doing hard work )

thias15, 2021-05-10:
Ok, great to hear it! If you figure out at some point what the issue was, it would be very helpful to know for others.

bender2po, 2021-05-10:
Sure, I will post here if I figure out the reason.

moneypi, 2021-05-26:
Hello, I met the same problem, any help?
Thanks!

bender2po, 2021-05-27:
@moneypi I am not expert in this field. This is what worked for me (and a workaround as well):
1. Installed the debug version of android app from here: https://github.com/intel-isl/OpenBot/actions/runs/818493537
2. Replaced some part of 'play_video' method in the VideoPlayer with below snippet
`    def play_video(self):
        if not self.stream:
            print(f'Sream not set')
            return
        print(f'Opening the stream...{self.stream}')
        cap = cv2.VideoCapture(self.stream)

        while(cap.isOpened()):
            ret, img = cap.read()
            #img = cv2.rotate(img, cv2.ROTATE_180)
            cv2.imshow('Video', img)
            cv2.waitKey(1)`
3. (optional) reduce pygame window size from setup_screen
4. Make sure your PC and phone are connected to same WiFi source
5. Open the debug app and select 'Free Roam'. On your PC: run the python code with '--video'. Now, you would see two pop-ups: one for stream and another for pygame control. You should select the pygame window to use keyboard control.
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

moneypi, 2021-05-27:
Thanks, my friend fix this for me.
He comment ```andGate.addCondition("camera permission");``` from https://github.com/intel-isl/OpenBot/blob/master/android/app/src/main/java/org/openbot/env/RtspServer.java and rebuild Android APP.
And I got Video Stream.

FYI, my phone is Redmi K30 5G/MIUI 12.1.8.

izivkov, 2021-05-27:
Hmm, you need camera permissions. You have bypassed it for now, but can
cause problems in the future.

The first think I would check is if the app has camera permissions from the
setup.

If not, you can set it manually. But I would uninstall the app, build it
again, and it should ask you to grant permission for the camera.

If not, you maybe running a pretty old version of Android. What is your
Android version.

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

moneypi, 2021-05-27:
Android Version 11
And，when running the app first time, I got the question: Take photos and record videos. And I select "Allow only while using the app".

I am not familiar with Android, maybe that's the reason.

izivkov, 2021-05-27:
Thanks, I'll check if the code has a problem with android 11.

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

moneypi, 2021-05-28:
My friend told me that is the problem of MIUI, which is different with the standard Android.

BaoAn21, 2025-04-03:
I see that this is a closed issue, but I face this and can not make it work, could anyone help me

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
I got to this point, and pygame was just freeze (you can see my mouse is loading) I need to force quit it because it was not run.
I use Samsung A06

BaoAn21, 2025-04-03:
I see that this is closed issue, but I face this and can not make it work.

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
I got to this point, and pygame was just freeze, I need to Force Quit the app, no video streaming happen
I use Samsung A06,
Could anyone help me? Thank you in advance

Closed 2021-05-10.

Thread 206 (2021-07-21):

ImageUtils.getScreenOrientation is not supported in older devices and causes crash

MohammedZ666, 2021-07-21:
The following method was updated [in this commit](https://github.com/intel-isl/OpenBot/commit/7e6b220f0988746f6ebdbdaea5a585e29b86f7b0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) to remove the depreciated call `activity.getWindowManager().getDefaultDisplay().getRotation()`  Unfortunately this crashes my device which has API 21. The call  `activity.getDisplay().getRotation()` requires API level 30:
```
public static int getScreenOrientation(Activity activity) {
    switch (activity.getDisplay().getRotation()) {
      case Surface.ROTATION_270:
        return 270;
      case Surface.ROTATION_180:
        return 180;
      case Surface.ROTATION_90:
        return 90;
      case Surface.ROTATION_0:
      default:
        return 0;
    }
  }
```
Can I replace this method with the following one?
```
public static int getScreenOrientation(Activity activity) {
    int rotation = Build.VERSION.SDK_INT >= Build.VERSION_CODES.R?
             activity.getDisplay().getRotation() : activity.getWindowManager().getDefaultDisplay().getRotation();
    switch (rotation) {
        case Surface.ROTATION_270:
          return 270;
        case Surface.ROTATION_180:
          return 180;
        case Surface.ROTATION_90:
          return 90;
        case Surface.ROTATION_0:
        default:
          return 0;

    }
  }
```
**Adding the above call fixes my problem.**

This is my logcat:
```
07-21 22:27:48.332 29430-29430/org.openbot E/AndroidRuntime: FATAL EXCEPTION: main
    Process: org.openbot, PID: 29430
    java.lang.NoSuchMethodError: No virtual method getDisplay()Landroid/view/Display; in class Landroid/app/Activity; or its super classes (declaration of 'android.app.Activity' appears in /system/framework/framework.jar)
        at org.openbot.env.ImageUtils.getScreenOrientation(ImageUtils.java:228)
        at org.openbot.common.CameraFragment.bindCameraUseCases(CameraFragment.java:102)
        at org.openbot.common.CameraFragment.setAnalyserResolution(CameraFragment.java:188)
        at org.openbot.autopilot.AutopilotFragment.onViewCreated(AutopilotFragment.java:116)
        at androidx.fragment.app.Fragment.performViewCreated(Fragment.java:2987)
        at androidx.fragment.app.FragmentStateManager.createView(FragmentStateManager.java:546)
        at androidx.fragment.app.FragmentStateManager.moveToExpectedState(FragmentStateManager.java:282)
        at androidx.fragment.app.FragmentManager.executeOpsTogether(FragmentManager.java:2189)
        at androidx.fragment.app.FragmentManager.removeRedundantOperationsAndExecute(FragmentManager.java:2106)
        at androidx.fragment.app.FragmentManager.execPendingActions(FragmentManager.java:2002)
        at androidx.fragment.app.FragmentManager$5.run(FragmentManager.java:524)
        at android.os.Handler.handleCallback(Handler.java:739)
        at android.os.Handler.dispatchMessage(Handler.java:95)
        at android.os.Looper.loop(Looper.java:148)
        at android.app.ActivityThread.main(ActivityThread.java:7223)
        at java.lang.reflect.Method.invoke(Native Method)
        at com.android.internal.os.ZygoteInit$MethodAndArgsCaller.run(ZygoteInit.java:1230)
        at com.android.internal.os.ZygoteInit.main(ZygoteInit.java:1120)
```
**This way older devices like mine may be supported. Thanks!**

thias15, 2021-07-21:
Please follow the [contribution guidelines](https://github.com/intel-isl/OpenBot/blob/master/CONTRIBUTING.md) to open a PR. You can then link this issue to it. Thank you very much!

MohammedZ666, 2021-07-21:
Thanks!

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

Closed 2021-07-21.

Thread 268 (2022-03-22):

openbot functionalities

robotixdevteam, 2022-03-22:
Today, controller app has crashed which has been downloaded from QR code. previously app is working we have faced bluetooth connection stability issues, is there any update for this issues???

thias15, 2022-03-22:
Can you please provide further details. @izivkov can you help @robotixdevteam to figure out a solution?

robotixdevteam, 2022-03-23:
sorry, now we have removed all the previous apps and installed new ones again now. They are installed.
But now we are facing mobiles are not getting connected to each other?

izivkov, 2022-03-23:
If you are talking about the controller phone not connecting to the robot
phone: make sure both phones are on the same LAN, not using data
connection. Make sure they are using the same router, i.e. not on a
University WiFi network, or something like that. Then try a few times,
sometimes they don't connect the first time.

If still doesn't work, please provide more information on what is going on
and your setup.

Thanks

On Wed, Mar 23, 2022, 12:23 AM robotixdevteam ***@***.***>
wrote:

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

robotixdevteam, 2022-03-23:
These are the steps we followed for connecting the mobiles.
connected the mobile to bot and open the apps in the mobile and change the control in viewer app to phone and have wait for some time. one more thing we connected the mobiles to same wifi connection. We have tried this many times still they are connected. I want to know whether the procedure for connecting is right or we are missing something to change?

robotixdevteam, 2022-03-23:
hi, another thing i would like to know is why you are using the arduino 33 iot, as the mobile has both wifi and bluetooth?

izivkov, 2022-03-23:
Ok, looks like you are doing the right steps, but also try the following:

1. Restart the Controller App on the right phone each time you are trying to connect
2. On the Main software, switch control between Gamepad and Phone a few times, The connection is getting initiated when the "Phone" control mode is selected.
3. Also, from the main screen, selected "Free Form" icon, and then switch the "Controller" icon (bottom left button) a few times.

Hope this helps

izivkov, 2022-03-23:
https://user-images.githubusercontent.com/4115966/159732255-eadd8d57-75c6-4a7a-ba94-0a46891d1a87.mp4

robotixdevteam, 2022-03-24:
is the phones are connected using the wifi or bluetooth?

thias15, 2022-03-28:
> ng about the controller phone not connecting to the robot phone: make sure both phones are on the same LAN, not using data connection. Make sure they are using the same router, i.e. not on a University WiFi network, or something like that. Then try a few times, sometimes they don't connect the first time.

This is just since the Arduino 33 IOT can be used also for other things. But it can work with Arduino Nano as well.

thias15, 2022-03-28:
There should not be a specific requirement for which phones can be used, but we did not test with the phones you mentioned above. You closed the issue, so I just wanted to check if the issue is resolved now from your end?

robotixdevteam, 2022-03-28:
No, the issue was not solved we are trying to understand where exactly is the problem if you have any ideas on how to solve it share with us?

robotixdevteam, 2022-03-28:
we wanted to open a new issue regarding it so we closed it

izivkov, 2022-03-28:
As I discussed with @robotixdevteam team last week, the problem seems to occur in only one of the phones: Redme. Since we cannot test all phones, we need to work together with the team on this issue. Maybe the team can provide some logs from this phone, to see if there are any crashes or what the problem is.

robotixdevteam, 2022-03-30:
we tested the node-js .while testing node-js, we came across certain issue of connectivity with some windows laptops. It is working good with raspberry pi and ubuntu os. currently, Have you tested the node-js with windows laptops. Right now, we are testing the python controller. Oh yes, i forgot to mention the main issue connectivity among two mobile phones that issue has not been solved from our side. Is there any updates regarding it.

robotixdevteam, 2022-03-30:
we tested the python code. some windows laptops there is connectivity issue and rest even though it is connected and popup-dialogue can  be seen but the video is not streaming through both RTSP and WEBRTC. We have not tested the python code as well as node-js in real time.

izivkov, 2022-03-30:
> we tested the python code. some windows laptops there is connectivity issue and rest even though it is connected and popup-dialogue can be seen but the video is not streaming through both RTSP and WEBRTC. We have not tested the python code as well as node-js in real time.

The Python controller works with RTSP video only.
Check and disable any firewall and virus protection on your Windows machines, maybe this will help.
The NodeJS and Python controllers have been developed on and for Linux-based OS's so far. It would be great if we can get them working on Windows, though.

robotixdevteam, 2022-03-31:
Prevously it connected to windows without video streaming but after disabling the protection and firewall it is not even getting connected.

thias15, 2022-04-28:
Any update on this?

izivkov, 2022-04-29:
This looks more like a configuration or a firewall issue. I think the same software works on some systems, but not on others. The Python controller was tested on Linux, and I left is as a "TO DO" to test on Windows, and recommend configuration. As of now, we cannot say that the Python controller is tested or supported on Windows. Since I am not running Windows on any of my machines, somebody can test it and let us know.

Closed 2022-04-29.

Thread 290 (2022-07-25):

Do you plan to support multicopters?

atolkachiov, 2022-07-25:
As far as I understand, there are plenty of pros to use smartphones as onboard computer for multicopters, for starters at least.
* sensors to maintain stable flight
* independent power source
* 4g connectivity
* ML-grade performance
* great price
* availability (which is often a blocker if you are going to make a build using some SBCs)

Do you have it on your roadmap? Looking for contributors?

thias15, 2022-07-26:
Hi @atolkachiov. We have considered it before, but there were a few concerns.
(1) People may be more hesitant to put their phone on a flying platform
(2) On quadrotors weight is a major concern and phones have quite a bit of extra weight due to battery, screen and chassis
(3) Integration of a full flight control stack in Android requires a lot of work

As a result the first priority has been ground vehicles. That being said, contributions would be most welcome.

atolkachiov, 2022-07-27:
Probably it would be easier to rely on Ardupilot compatible SoC as a flight controller and have smartphone as an auxiliary [companion computer](https://ardupilot.org/dev/docs/companion-computers.html) module focused on ML tasks and autonomous flight. As Ardupilot supports Odroid boards which run Android, adding multirotors supports may essentially be introducing MAVLink protocol bridge API available for the user app.

I understand all the concerns, but professional turnkey solutions cost a fortune and even then often they are not available because of chip shortage. Having some extra weight onboard sounds like an acceptable tradeoff If you can get powerful GPU + quality cameras + lidar + cellular connectivity for a few hundreds dollars. Good for learning and prototyping.

thias15, 2022-10-13:
Hi @atolkachiov. I'm closing this for now since this is not a high priority on our roadmap and we have very limited bandwidth. However, if you would be interested to work on this we would be happy to support as much as we can!

Closed 2022-10-13.

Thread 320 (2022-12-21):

Bot react on voice commands ?

reger24, 2022-12-21:
Hi @thias15 ,

**would you accept a pull request for implementing of a voice recognition feature** into the android app, so bot can react on voice commands or is that out of scope **?**

**Describe**
The idea is, to use the ML example ("[TensorFlow Lite Speech Command Recognition Android Demo](https://github.com/tensorflow/examples/tree/189c662d500c20b9f9e93fef0af97d5311e64377/lite/examples/speech_commands/android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)") which can recognize (out-of-the-box) "yes, no, up, down, left, right, on, off, stop, go" as a starting point.
I'd implement it in a way that it can be activated (or is active) in the auto-modes so the user can interfere with the controls by a voice command e.g. "stop" to overwrite/correct bot steering/speeds to perform a emergency stop or to have the bot rotate to find the object for tracking etc......
My preference would be to implement it as service so it can be used (activated) from/for any activity.

reger24, 2022-12-21:
OK, then I'll start coding.
cu

izivkov, 2022-12-21:
@reger24 How do you plan to do it? Would it be part of the main app or would it reside on another device, acting as a controller? I think both are valid options, but if it is separate phone, you don't have to shout at the robot. ;-)

reger24, 2022-12-21:
@izivkov My plan is to make it part of the main app (so you would need to shout at the robot) !
Was also thinking about it as feature or replacement for the phonecontroller, but discarded the idea,
because my interest is to have a way to influence the robot mainly during auto-modes, not to replace the joystick.

izivkov, 2022-12-21:
👍

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

reger24, 2022-12-23:
fyi: progress can be viewed in clone branch https://github.com/reger24/OpenBot/tree/VoiceRecognition

(as it may take some days and commits before ready for a pull request).

reger24, 2022-12-27:
fyi: first testing went not very well,
due to the (higher as expected) negative effect of noise level from bot motors.
After a start command barely any following voice command is recognized.
've to see if I find a tweak to overcome this hurdle.

izivkov, 2022-12-27:
I'm also not sure about the latency. I have no experience with how fast
voice commands are interpreted, but I imagine there would be some delay in
processing them. Having worked on the various remote controllers for the
bot, I know repeated steering commands need to be sent in fast succession
for good performance. But don't let me discourage your development. I think
it would be a great feature if we can implement it.

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

reger24, 2022-12-27:
@izivkov Thanks for your hint and encouragement,
but the issue during first testing was/is the background noise the motors make while driving and the voice recognition apparently too sensitive to background noise/sounds so the recognition itself doesn't work well as it does in quiet environment (with the given neural network).
Currently I see still some options to try, 've to see if it improves it enough for an acceptable workaround.

reger24, 2023-02-08:
### fyi - giving up on unsolved motor noise problem - for a direct robot app voice recognition

The noise from robot's motors is a bigger problem as anticipated,
because the microphone is very close to the motors, so that this noise dominates the recording.
The motor noise is as loud as the voice if one shouts at the robot from close distance.

I experimented with different noise filters to eliminate/reduce the motor noise without success,
as the frequencies overlap with the voice command frequencies, with the result that recording quality is not high enough for recognition.

Tried filters are
- lowpass, highpass, bandpass/-reject filter from [marytts.signalproc.filter](https://github.com/marytts/marytts/tree/master/marytts-signalproc/src/main/java/marytts/signalproc/filter)
- and [rnnoise4j library](https://github.com/henkelmax/rnnoise4j) (w/o specific training data)
as said without success.

I end up with last option, using voice recognition only if robot doesn't move or via a distant microphone.
Both not intended (by me) at this time for the small command set that comes with the used voice recognition sample ,
so I'll stop working on this feature for now.

thias15, 2023-02-08:
Hi @reger24 that's too bad. How about connecting a BT headset to the phone? Then you can just talk into the microphone and will avoid all of these noise issues.

reger24, 2023-02-09:
Now, as I found the manual of my BT headset how to bring it in pairing mode to connect to robot's phone,
I'll give it a try with your suggestion (and see if I can get far enough away from the crying motors ;-)

reger24, 2023-02-10:
Hi @thias15,   short feedback on your input:
first rudimentary testing shows the suggested BT headset workaround could work. at least voice commands where recognized (not all the time but much better as before),
so worsewhile to spend a bit more time for further testing and tuning.
cu

thias15, 2023-02-11:
If you are standing a few meters away and microphone is close to your face it should be fine. Another option is to use a different motor, for example the 520. It makes less noise.

Closed 2023-02-08.

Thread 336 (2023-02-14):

[DIY] Nano board freeze and stop accepting commands after starting the motor with c command.

shashank734, 2023-02-14:
Hey Folks, Building DIY and Connected the Arduino nano with the studio, Uploaded the firmware it's connected and showed the data on OLED and serial monitor both. when I send the i0,1, i1,0 ... commands, it's working fine.

But when I send the c command motor starts, but OLED turns off, and it stops sending the data on the serial monitor, it stops accepting the commands need to unplug the USB and insert it again to stop the motor. Turn on/off the power switch without removing the USB. still, motor starts and not accepting commands to make it work need to remove the USB. I think the board freezes after sending motor commands. Tried with Not connected to the phone yet.

The same is happening with the phone App; after starting the motor, no other commands working need to reconnect.

PS: I observe with the phone it was accepting the instructions when the motor was at a slow speed once the motor is at high-speed everything gets freeze.

Using this board https://robu.in/product/arduino-nano-board-r3-ch340-chip-with-usb-cable-solderedarduino-nano-r3-usb-cable/

Thanks for great project :)

thias15, 2023-02-14:
Hi @shashank734. It sounds like the electric noise of the motors might be causing interference. Can you try to shield the USB cable and keep it as far as possible from the motor wires? Another reason could be a faulty board (but then it's weird why it works for low motor speeds), especially the cheap Arduino clones are not always reliable.

shashank734, 2023-02-16:
Hi @thias15, Thanks for the response will try this on the weekend and update here. Actually, it's only sometimes working at a slow speed; it worked only a few times for a few seconds than stuck.

shashank734, 2023-02-19:
Hey tried to put Arduino at distance from the motor, and then it works but after some time again freezes. Maybe an issue with Arduino but don't know why it's working sometimes by putting it at a distance.

thias15, 2023-03-03:
Hard to debug remotely. Would recommend trying a new/different Arduino board.

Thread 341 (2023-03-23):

Build an expanded version of the DIY version available for most popular 3D printers

Christos-Ps, 2023-03-23:
Since i build my first DIY Openbot this week using the published 3d stl files (https://github.com/isl-org/OpenBot/tree/master/body/diy/cad), i realized that the following problems could be adressed:

1. Most popular 3D printers (like the Ender 3 i used) have a usable print area of 220 x 220 mm. However, the size of the build surface actually measures 235 x 235 mm which can be used for the "Slim_Body" only version. Unfortunately the "Slim_Body" version lacks the most valuable bumpers that the "Regular_Body" provides.
3. More over I am afraid that the available space inside the DIY version of the bot is very limited, resulting in:

- cabling difficulty
- preventing any hardware future expansion connectivity, since even if you decide to use extra sensors there is no space inside the shell
- assembly difficulty, especially when you need to need to fix connectors that were removed due to cable stress on assembly

As a result:
I have redesigned the bottom and top stl trying to get the best of both worlds, since i would like to avoid the "glued" version for structural integrity reasons.
What i did was the following:

1. I used the "Regular_Body" version as a template
2. I replaced the back bumper with a slim one
3. I reduced the wheelbase to bumper dimension
4. I created a top cover height towards the half of the openbot, resulting to almost double height from center to back.
5. As an extra cherry to the pie (after my kids request) i created an extra version with lego combatible bricks patch on top of the back to be able to let them play & learn robotics.

I am attaching some screenshots if you like it and also agree that it could help others!
On the next step i will upload the stl files according to your guidelines
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

Best regards
Christos

Christos-Ps, 2023-03-23:
Hi @thias15

I have uploaded all stl+readme file in Pull request #342 and i closed the request
https://github.com/isl-org/OpenBot/pull/342
Please let me know if i missed any step needed for the folder creation

Cheers!

Christos-Ps, 2023-03-27:
Hi @thias15
Is the #342 working for you, or i shouldn't have closed it prior to review?

Cheers

Closed 2023-04-06.

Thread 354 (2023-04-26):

Unpowered arduino nano

rfedersp, 2023-04-26:
Hi, I'm a total beginner in electronics and I'm trying to build the DIY version of OpenBot (which is a great project!). The problem is that I can't power the Arduino Nano with the voltage divider bridge... Is my assembly wrong?

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

thias15, 2023-04-26:
Hard to tell from the image but looks roughly ok. Can you measure the voltage with a multimeter? Note that if you built the voltage divider as per instructions and connected it to the corresponding pins the purpose is not to power the Arduino but to measure the battery voltage. The Arduino is powered via the USB connection to the phone.

rfedersp, 2023-04-27:
I measure a voltage of 0.6 but it must be normal if it is not intended to power the arduino.
On the other hand, when I connect my phone to the arduino, no led lights up, is that normal?

rfedersp, 2023-04-27:
The problem was with my OTG cable... Everything works now!
Thank you for your help :)

Closed 2023-04-27.

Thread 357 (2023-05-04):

NodeMCU ESP32s

lechfak, 2023-05-04:
Hello.
I want to make DİY_ESP32 with NodeMCU ESP32s.
I used L298 as motor driver.

Where should I connect the CH_PWM_L1/ L2/R1/R2 and PIN_PWM_LF1/LB1... pins? I don't understand this.
When CH_PWM_L1 remains as is, all engines are running in NO_PHONE mode only. But none of them work in normal mode.

When I do the same with CH_PWM_... and PIN_PWM_.LF/LB.., only the motors on the left respond to commands.
//PWM properties
const int FREQ = 5000;
const int RES = 8;
const int CH_PWM_L1 =13;
const int CH_PWM_L2 = 12;
const int CH_PWM_R1 = 27;
const int CH_PWM_R2 = 33
const int PIN_PWM_LF1 = 13;
const int PIN_PWM_LF2 = 12;
const int PIN_PWM_LB1 = 13;
const int PIN_PWM_LB2 = 12;
const int PIN_PWM_RF1 = 27;
const int PIN_PWM_RF2 = 33;
const int PIN_PWM_RB1 = 27;
const int PIN_PWM_RB2 = 33;

What can I do?

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

thias15, 2023-05-04:
Please use the latest firmware. The `CH_PWM` can just have values 0,1,2,3. The physical GPIO pins are defined as `PIN_PWM_LF1`, `PIN_PWM_LB1`, etc. Note that LF (left front) and LB (left back) are defined as the same pin since we only have two outputs - one for the left side and the other for the right side. You should connect pins 13 and 12 to IN1 and IN2 to control the left side and pins 27 and 33 to IN3 and IN4 to control the right side.

thias15, 2023-05-04:
If it works in the No_PHONE mode, it means that the wiring is correct. It seems the issue you are facing is with the connection between robot and phone then. Did you try to send commands from the serial monitor in Arduino? Does the robot info screen work when the robot is connected?

lechfak, 2023-05-05:
Hi.
1.  yes. i try to send commands from the serial monitor in Arduino. wıth c255,255. but there is no change
2. robot info screen dont work when the robot is connected
![WhatsApp Image 2023-05-05 at 14 41 33 (1)](https://user-images.githubuserconten
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
t.com/24843137/236449220-bd0543d9-e887-4c8c-8ffc-2f94f8914491.jpeg)
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

lechfak, 2023-05-09:
Hi.
I was able to connect to the device using bluetooth connection.
It didn't happen with the USB cable at the same settings.
The robot info screen has seen the device.
but after working for a few seconds, the device turns itself off by giving this error:

Guru Meditation Error: Core  1 panic'ed (InstrFetchProhibited). Exception was unhandled.
Core 1 register dump:
PC      : 0x00000000  PS      : 0x00060130  A0      : 0x800d14e9  A1      : 0x3ffcafc0
A2      : 0x3ffc45f8  A3      : 0x00000000  A4      : 0x0000aeb4  A5      : 0x0000da80
A6      : 0x00000020  A7      : 0x3ffc90e0  A8      : 0x800d6caf  A9      : 0x3ffcafa0
A10     : 0x3ffc45f8  A11     : 0x3ffba660  A12     : 0x00000005  A13     : 0x00000005
A14     : 0x00000003  A15     : 0x00060023  SAR     : 0x0000000a  EXCCAUSE: 0x00000014
EXCVADDR: 0x00000000  LBEG    : 0x4000c28c  LEND    : 0x4000c296  LCOUNT  : 0x00000000

ELF file SHA256: 0000000000000000

Backtrace: 0x00000000:0x3ffcafc0 0x400d14e6:0x3ffcafe0 0x400d1586:0x3ffcb000 0x400d860c:0x3ffcb020 0x400905de:0x3ffcb040

Rebooting...
ets Jun  8 2016 00:22:57

rst:0xc (SW_CPU_RESET),boot:0x13 (SPI_FAST_FLASH_BOOT)
configsip: 0, SPIWP:0xee
clk_drv:0x00,q_drv:0x00,d_drv:0x00,cs0_drv:0x00,hd_drv:0x00,wp_drv:0x00
mode:DIO, clock div:1
load:0x3fff0018,len:4
load:0x3fff001c,len:1216
ho 0 tail 12 room 4
load:0x40078000,len:10944
load:0x40080400,len:6388
entry 0x400806b4

hardikgarg02, 2023-09-15:
Hey! Which Android device have you used for connecting to the robot? If connecting via USB and the serial monitor is not sending commands to the robot, try using a different device for the connection.

hemangjoshi37a, 2024-10-14:
I am using the defualt firmware file and getting this error in my esp32 devkit v1 :
```
17:29:17.656 -> rst:0x8 (TG1WDT_SYS_RESET),boot:0x13 (SPI_FAST_FLASH_BOOT)
17:29:17.656 -> configsip: 0, SPIWP:0xee
17:29:17.656 -> clk_drv:0x00,q_drv:0x00,d_drv:0x00,cs0_drv:0x00,hd_drv:0x00,wp_drv:0x00
17:29:17.656 -> mode:DIO, clock div:1
17:29:17.656 -> load:0x3fff0030,len:4832
17:29:17.656 -> load:0x40078000,len:16460
17:29:17.656 -> load:0x40080400,len:4
17:29:17.656 -> load:0x40080404,len:3504
17:29:17.656 -> entry 0x400805cc
17:29:18.399 -> ets Jul 29 2019 12:21:46
```

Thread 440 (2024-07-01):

Unable to complile code for ESP32.

Getafix17, 2024-07-01:
I successfully compiled and uploaded the code to an Arduino Nano; however,, I am struggling to compile the code to ESP32.
I have included all the necessary libraries for ESP32 and BLE. I will be using an L298n an Android phone and a ESP32.
Perhaps I missed something.
My config for ESP32 in Arduino IDE:
//MCUs
 #define NANO 328 //Atmega328p
 #define ESP32 32 //ESP32

//Robot bodies with Atmega328p as MCU --> Select Arduino Nano as board
  #define DIY 0        // DIY without PCB
  #define PCB_V1 1     // DIY with PCB V1
  #define PCB_V2 2     // DIY with PCB V2
  #define RTR_TT 3     // Ready-to-Run with TT-motors
  #define RC_CAR 4     // RC truck prototypes
  #define LITE 5       // Smaller DIY version for education
//Robot bodies with ESP32 as MCU --> Select ESP32 Dev Module as board
  #define RTR_TT2 6   // Ready-to-Run with TT-motors
  #define RTR_520 7    // Ready-to-Run with 520-motors
  #define MTV 8        // Multi Terrain Vehicle
  #define DIY_ESP32 9  // DIY without PCB

//------------------------------------------------------//
// SETUP - Choose your body
//------------------------------------------------------//

// Setup the OpenBot version (DIY, PCB_V1, PCB_V2, RTR_TT, RC_CAR, LITE, RTR_TT2, RTR_520, DIY_ESP32,OPENBOT DIY)
#define OPENBOT DIY_ESP32

SETTINGS - Global settings
//------------------------------------------------------//

// Enable/Disable no phone mode (1,0)
// In no phone mode:
// - the motors will turn at 75% speed
// - the speed will be reduced if an obstacle is detected by the sonar sensor
// - the car will turn, if an obstacle is detected within TURN_DISTANCE
// WARNING: If the sonar sensor is not setup, the car will go full speed forward!
#define NO_PHONE_MODE 1

// Enable/Disable debug print (1,0)
#define DEBUG 1

// Enable/Disable coast mode (1,0)
// When no control is applied, the robot will either coast (1) or actively stop (0)
boolean coast_mode = 0;

My snippet for DIY ESP32
//-------------------------DIY_ESP32----------------------//
#elif (OPENBOT == DIY_ESP32)
const String robot_type = "DIY_ESP32";
#define MCU ESP32
#include <esp_wifi.h>
#define HAS_BLUETOOTH 1
#define analogWrite ledcWrite
#define attachPinChangeInterrupt attachInterrupt
#define detachPinChangeInterrupt detachInterrupt
#define digitalPinToPinChangeInterrupt digitalPinToInterrupt
#define PIN_PWM_L1 CH_PWM_L1
#define PIN_PWM_L2 CH_PWM_L2
#define PIN_PWM_R1 CH_PWM_R1
#define PIN_PWM_R2 CH_PWM_R2
#define HAS_VOLTAGE_DIVIDER 0
const float VOLTAGE_DIVIDER_FACTOR = (30 + 10) / 10;
const float VOLTAGE_MIN = 6.0f;
const float VOLTAGE_LOW = 9.0f;
const float VOLTAGE_MAX = 12.6f;
const float ADC_FACTOR = 3.3 / 4095;
#define HAS_INDICATORS 0
#define HAS_SONAR 0
#define SONAR_MEDIAN 0
#define HAS_SPEED_SENSORS_FRONT 0
//PWM properties
const int FREQ = 5000;
const int RES = 8;
const int CH_PWM_L1 = 0;
const int CH_PWM_L2 = 1;
const int CH_PWM_R1 = 2;
const int CH_PWM_R2 = 3;
const int PIN_PWM_LF1 = 13;
const int PIN_PWM_LF2 = 12;
const int PIN_PWM_LB1 = 13;
const int PIN_PWM_LB2 = 12;
const int PIN_PWM_RF1 = 27;
const int PIN_PWM_RF2 = 33;
const int PIN_PWM_RB1 = 27;
const int PIN_PWM_RB2 = 33;
const int PIN_SPEED_LF = 5;
const int PIN_SPEED_RF = 18;
const int PIN_VIN = 39;
const int PIN_TRIGGER = 25;
const int PIN_ECHO = 26;
const int PIN_LED_LI = 22;
const int PIN_LED_RI = 16;
#endif

 The error:
 Used: C:\Users\alexf\Documents\Arduino\libraries\ESP32_BLE_Arduino
 Not used: C:\Users\alexf\AppData\Local\Arduino15\packages\esp32\hardware\esp32\3.0.2\libraries\BLE
exit status 1
'ledcSetup' was not declared in this scope

thias15, 2024-07-01:
Try using version 2.x of Arduino-ESP32 since there were some [breaking changes](https://github.com/espressif/arduino-esp32/blob/master/docs/en/migration_guides/2.x_to_3.0.rst#ledc).

Closed 2024-07-01.

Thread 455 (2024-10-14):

getting this error in esp32

hemangjoshi37a, 2024-10-14:
```

17:28:34.751 -> rst:0x8 (TG1WDT_SYS_RESET),boot:0x13 (SPI_FAST_FLASH_BOOT)
17:28:34.751 -> configsip: 0, SPIWP:0xee
17:28:34.751 -> clk_drv:0x00,q_drv:0x00,d_drv:0x00,cs0_drv:0x00,hd_drv:0x00,wp_drv:0x00
17:28:34.784 -> mode:DIO, clock div:1
17:28:34.784 -> load:0x3fff0030,len:4832
17:28:34.784 -> load:0x40078000,len:16460
17:28:34.784 -> load:0x40080400,len:4
17:28:34.784 -> load:0x40080404,len:3504
17:28:34.784 -> entry 0x400805cc
17:28:35.526 -> ets Jul 29 2019 12:21:46
```

getting this error in esp32 by uploading the default firmware arduino file without any changes .

isha382, 2024-10-14:
Hi @hemangjoshi37a, You need to change this line  if (OPENBOT == DIY) to if(OPENBOT == DIY_ESP32) in the arduino file then you can upload.
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

hemangjoshi37a, 2024-10-14:
now i am getting this error :
```
/home/hemang/Documents/GitHub/OpenBot/firmware/openbot/openbot.ino: In function 'void setup()':
/home/hemang/Documents/GitHub/OpenBot/firmware/openbot/openbot.ino:906:3: error: 'ledcSetup' was not declared in this scope; did you mean 'ledc_stop'?
  906 |   ledcSetup(CH_PWM_L1, FREQ, RES);
      |   ^~~~~~~~~
      |   ledc_stop
/home/hemang/Documents/GitHub/OpenBot/firmware/openbot/openbot.ino:912:3: error: 'ledcAttachPin' was not declared in this scope; did you mean 'ledcAttach'?
  912 |   ledcAttachPin(PIN_PWM_LF1, CH_PWM_L1);
      |   ^~~~~~~~~~~~~
      |   ledcAttach

exit status 1

Compilation error: 'ledcSetup' was not declared in this scope; did you mean 'ledc_stop'?
```

hemangjoshi37a, 2024-10-14:
here is my final working code :
```c
#include <Arduino.h>
#include "driver/ledc.h"

const String robot_type = "DIY_ESP32";
// Required App Version: 0.7.0
// ---------------------------------------------------------------------------
// This Arduino Nano sketch accompanies the OpenBot Android application.
//
// The sketch has the following functionalities:
//  - receive control commands and sensor config from Android application (USB serial)
//  - produce low-level controls (PWM) for the vehicle
//  - toggle left and right indicator signals
//  - wheel odometry based on optical speed sensors
//  - estimate battery voltage via voltage divider
//  - estimate distance based on sonar sensor
//  - control LEDs for status and at front and back of vehicle
//  - send sensor readings to Android application (USB serial)
//  - display vehicle status on OLED
//
// Dependencies: Install via "Tools --> Manage Libraries" (type library name in the search field)
//  - Interrupts: PinChangeInterrupt by Nico Hood (read speed sensors and sonar)
//  - OLED: Adafruit_SSD1306 & Adafruit_GFX (display vehicle status)
//  - Servo: Built-In library by Michael Margolis (required for RC truck)
// Contributors:
//  - October 2020: OLED display support by Ingmar Stapel
//  - December 2021: RC truck support by Usman Fiaz
//  - March 2022: OpenBot-Lite support by William Tan
//  - May 2022: MTV support by Quentin Leboutet
//  - Jan 2023: BLE support by iTinker
// ---------------------------------------------------------------------------

// By Matthias Mueller, 2023
// ---------------------------------------------------------------------------

//------------------------------------------------------//
// DEFINITIONS - DO NOT CHANGE!
//------------------------------------------------------//

//MCUs
#define NANO 328 //Atmega328p
#define ESP32 32 //ESP32

//Robot bodies with Atmega328p as MCU --> Select Arduino Nano as board
#define DIY 0        // DIY without PCB
#define PCB_V1 1     // DIY with PCB V1
#define PCB_V2 2     // DIY with PCB V2
#define RTR_TT 3     // Ready-to-Run with TT-motors
#define RC_CAR 4     // RC truck prototypes
#define LITE 5       // Smaller DIY version for education
//Robot bodies with ESP32 as MCU --> Select ESP32 Dev Module as board
#define RTR_TT2 6   // Ready-to-Run with TT-motors
#define RTR_520 7    // Ready-to-Run with 520-motors
#define MTV 8        // Multi Terrain Vehicle
#define DIY_ESP32 9  // DIY without PCB

//------------------------------------------------------//
// SETUP - Choose your body
//------------------------------------------------------//

// Setup the OpenBot version (DIY, PCB_V1, PCB_V2, RTR_TT, RC_CAR, LITE, RTR_TT2, RTR_520, DIY_ESP32)
#define OPENBOT DIY_ESP32

//------------------------------------------------------//
// SETTINGS - Global settings
//------------------------------------------------------//

// Enable/Disable no phone mode (1,0)
// In no phone mode:
// - the motors will turn at 75% speed
// - the speed will be reduced if an obstacle is detected by the sonar sensor
// - the car will turn, if an obstacle is detected within TURN_DISTANCE
// WARNING: If the sonar sensor is not setup, the car will go full speed forward!
#define NO_PHONE_MODE 0

// Enable/Disable debug print (1,0)
#define DEBUG 0

// Enable/Disable coast mode (1,0)
// When no control is applied, the robot will either coast (1) or actively stop (0)
bool coast_mode = 1;

//------------------------------------------------------//
// CONFIG - update if you have built the DIY version
//------------------------------------------------------//
// HAS_VOLTAGE_DIVIDER                  Enable/Disable voltage divider (1,0)
// VOLTAGE_DIVIDER_FACTOR               The voltage divider factor is computed as (R1+R2)/R2
// HAS_INDICATORS                       Enable/Disable indicators (1,0)
// HAS_SONAR                            Enable/Disable sonar (1,0)
// SONAR_MEDIAN                         Enable/Disable median filter for sonar measurements (1,0)
// HAS_BUMPER                           Enable/Disable bumper (1,0)
// HAS_SPEED_SENSORS_FRONT              Enable/Disable front speed sensors (1,0)
// HAS_SPEED_SENSORS_BACK               Enable/Disable back speed sensors (1,0)
// HAS_SPEED_SENSORS_MIDDLE             Enable/Disable middle speed sensors (1,0)
// HAS_OLED                             Enable/Disable OLED display (1,0)
// HAS_LEDS_FRONT                       Enable/Disable front LEDs
// HAS_LEDS_BACK                        Enable/Disable back LEDs
// HAS_LEDS_STATUS                      Enable/Disable status LEDs
// HAS_BLUETOOTH                        Enable/Disable bluetooth connectivity (1,0)
// NOTE: HAS_BLUETOOTH will only work with the ESP32 board (RTR_TT2, RTR_520, MTV, DIY_ESP32)

// PIN_TRIGGER                          Arduino pin tied to trigger pin on ultrasonic sensor.
// PIN_ECHO                             Arduino pin tied to echo pin on ultrasonic sensor.
// MAX_SONAR_DISTANCE                   Maximum distance we want to ping for (in centimeters).
// PIN_PWM_T                            Low-level control of throttle via PWM (for OpenBot RC only)
// PIN_PWM_S                            Low-level control of steering via PWM (for OpenBot RC only)
// PIN_PWM_L1,PIN_PWM_L2                Low-level control of left DC motors via PWM
// PIN_PWM_R1,PIN_PWM_R2                Low-level control of right DC motors via PWM
// PIN_VIN                              Measure battery voltage via voltage divider
// PIN_SPEED_LB, PIN_SPEED_RB           Measure left and right back wheel speed
// PIN_SPEED_LF, PIN_SPEED_RF           Measure left and right front wheel speed
// PIN_LED_LB, PIN_LED_RB               Control left and right back LEDs (indicator signals, illumination)
// PIN_LED_LF, PIN_LED_RF               Control left and right front LEDs (illumination)
// PIN_LED_Y, PIN_LED_G, PIN_LED_B      Control yellow, green and blue status LEDs

//-------------------------DIY--------------------------//
#if (OPENBOT == DIY)
const String robot_type = "DIY";
#define MCU NANO
#define HAS_VOLTAGE_DIVIDER 0
const float VOLTAGE_DIVIDER_FACTOR = (20 + 10) / 10;
const float VOLTAGE_MIN = 2.5f;
const float VOLTAGE_LOW = 9.0f;
const float VOLTAGE_MAX = 12.6f;
const float ADC_FACTOR = 5.0 / 1023;
#define HAS_INDICATORS 0
#define HAS_SONAR 0
#define SONAR_MEDIAN 0
#define HAS_SPEED_SENSORS_FRONT 0
#define HAS_OLED 0
const int PIN_PWM_L1 = 5;
const int PIN_PWM_L2 = 6;
const int PIN_PWM_R1 = 9;
const int PIN_PWM_R2 = 10;
const int PIN_SPEED_LF = 2;
const int PIN_SPEED_RF = 3;
const int PIN_VIN = A7;
const int PIN_TRIGGER = 12;
const int PIN_ECHO = 11;
const int PIN_LED_LI = 4;
const int PIN_LED_RI = 7;

//-------------------------PCB_V1-----------------------//
#elif (OPENBOT == PCB_V1)
const String robot_type = "PCB_V1";
#define MCU NANO
#define HAS_VOLTAGE_DIVIDER 1
const float VOLTAGE_DIVIDER_FACTOR = (100 + 33) / 33;
const float VOLTAGE_MIN = 2.5f;
const float VOLTAGE_LOW = 9.0f;
const float VOLTAGE_MAX = 12.6f;
const float ADC_FACTOR = 5.0 / 1023;
#define HAS_INDICATORS 1
#define HAS_SONAR 1
#define SONAR_MEDIAN 0
#define HAS_SPEED_SENSORS_FRONT 1
#define HAS_OLED 0
const int PIN_PWM_L1 = 9;
const int PIN_PWM_L2 = 10;
const int PIN_PWM_R1 = 5;
const int PIN_PWM_R2 = 6;
const int PIN_SPEED_LF = 2;
const int PIN_SPEED_RF = 4;
const int PIN_VIN = A7;
const int PIN_TRIGGER = 3;
const int PIN_ECHO = 3;
const int PIN_LED_LI = 7;
const int PIN_LED_RI = 8;

//-------------------------PCB_V2-----------------------//
#elif (OPENBOT == PCB_V2)
const String robot_type = "PCB_V2";
#define MCU NANO
#define HAS_VOLTAGE_DIVIDER 1
const float VOLTAGE_DIVIDER_FACTOR = (20 + 10) / 10;
const float VOLTAGE_MIN = 2.5f;
const float VOLTAGE_LOW = 9.0f;
const float VOLTAGE_MAX = 12.6f;
const float ADC_FACTOR = 5.0 / 1023;
#define HAS_INDICATORS 1
#define HAS_SONAR 1
#define SONAR_MEDIAN 0
#define HAS_SPEED_SENSORS_FRONT 1
#define HAS_OLED 0
const int PIN_PWM_L1 = 9;
const int PIN_PWM_L2 = 10;
const int PIN_PWM_R1 = 5;
const int PIN_PWM_R2 = 6;
const int PIN_SPEED_LF = 2;
const int PIN_SPEED_RF = 3;
const int PIN_VIN = A7;
const int PIN_TRIGGER = 4;
const int PIN_ECHO = 4;
const int PIN_LED_LI = 7;
const int PIN_LED_RI = 8;

//-------------------------RTR_TT-----------------------//
#elif (OPENBOT == RTR_TT)
const String robot_type = "RTR_TT";
#define MCU NANO
#define HAS_VOLTAGE_DIVIDER 1
const float VOLTAGE_DIVIDER_FACTOR = (30 + 10) / 10;
const float VOLTAGE_MIN = 2.5f;
const float VOLTAGE_LOW = 9.0f;
const float VOLTAGE_MAX = 12.6f;
const float ADC_FACTOR = 5.0 / 1023;
#define HAS_INDICATORS 1
#define HAS_SONAR 1
#define SONAR_MEDIAN 0
#define HAS_BUMPER 1
#define HAS_SPEED_SENSORS_FRONT 1
#define HAS_SPEED_SENSORS_BACK 1
#define HAS_LEDS_FRONT 1
#define HAS_LEDS_BACK 1
#define HAS_LEDS_STATUS 1
const int PIN_PWM_L1 = 10;
const int PIN_PWM_L2 = 9;
const int PIN_PWM_R1 = 6;
const int PIN_PWM_R2 = 5;
const int PIN_SPEED_LF = A3;
const int PIN_SPEED_RF = 7;
const int PIN_SPEED_LB = A4;
const int PIN_SPEED_RB = 8;
const int PIN_VIN = A6;
const int PIN_TRIGGER = 4;
const int PIN_ECHO = 2;
const int PIN_LED_LI = A5;
const int PIN_LED_RI = 12;
const int PIN_LED_LB = A5;
const int PIN_LED_RB = 12;
const int PIN_LED_LF = 3;
const int PIN_LED_RF = 11;
const int PIN_LED_Y = 13;
const int PIN_LED_G = A0;
const int PIN_LED_B = A1;
const int PIN_BUMPER = A2;
const int BUMPER_NOISE = 512;
const int BUMPER_EPS = 10;
const int BUMPER_AF = 951;
const int BUMPER_BF = 903;
const int BUMPER_CF = 867;
const int BUMPER_LF = 825;
const int BUMPER_RF = 786;
const int BUMPER_BB = 745;
const int BUMPER_LB = 607;
const int BUMPER_RB = 561;

//-------------------------RC_CAR-----------------------//
#elif (OPENBOT == RC_CAR)
const String robot_type = "RC_CAR";
#define MCU NANO
#include <Servo.h>
Servo ESC;
Servo SERVO;
#define HAS_VOLTAGE_DIVIDER 0
const float VOLTAGE_DIVIDER_FACTOR = (20 + 10) / 10;
const float VOLTAGE_MIN = 0.0f;
const float VOLTAGE_LOW = 6.4f;
const float VOLTAGE_MAX = 8.4f;
const float ADC_FACTOR = 5.0 / 1023;
#define HAS_INDICATORS 0
#define HAS_SONAR 0
#define SONAR_MEDIAN 0
const int PIN_PWM_T = A0;
const int PIN_PWM_S = A1;
const int PIN_VIN = A7;
const int PIN_TRIGGER = 4;
const int PIN_ECHO = 4;
const int PIN_LED_LI = 7;
const int PIN_LED_RI = 8;
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

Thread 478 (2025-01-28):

Speed sensors issue.

tbellembois, 2025-01-28:
Hello,

I have an issue with my speed sensor. Only one reports speed for both right and left.
If I only run the left wheels the OLED display gives the same speed for both right and left wheels.
If I only run the right wheels the OLED display gives 0 rpm.

I have checked my wiring three times. I have tested with the Android application and Arduino console.

Desktop: linux Fedora 42
Smartphone: Sony xperia xa2 for the bot, Volla phone 22 for the controller

DIY version.

Here is my firmware configuration (relevant part only):
```
#define OPENBOT DIY
...
//-------------------------DIY--------------------------//
#if (OPENBOT == DIY)
const String robot_type = "DIY";
#define MCU NANO
#define HAS_VOLTAGE_DIVIDER 1
const float VOLTAGE_DIVIDER_FACTOR = (20 + 10) / 10;
const float VOLTAGE_MIN = 2.5f;
const float VOLTAGE_LOW = 9.0f;
const float VOLTAGE_MAX = 12.6f;
const float ADC_FACTOR = 5.0 / 1023;
#define HAS_INDICATORS 1
#define HAS_SONAR 1
#define SONAR_MEDIAN 0
#define HAS_SPEED_SENSORS_FRONT 1
#define HAS_OLED 1
const int PIN_PWM_L1 = 5;
const int PIN_PWM_L2 = 6;
const int PIN_PWM_R1 = 9;
const int PIN_PWM_R2 = 10;
const int PIN_SPEED_LF = 2;
const int PIN_SPEED_RF = 3;
const int PIN_VIN = A7;
const int PIN_TRIGGER = 12;
const int PIN_ECHO = 11;
const int PIN_LED_LI = 4;
const int PIN_LED_RI = 7;
```

Any idea? Thanks for your help.

tbellembois, 2025-01-29:
Update: after more tests the Arduino console reports correct values. This is an oled display issue.

tbellembois, 2025-01-29:
I found the issue, in the firmware file, line 1622:
```
String right_rpm_str = String("Right RPM:  ") + String(rpm_left, 0);
```
just replaced `rpm_left` with `rpm_left`.

thias15, 2025-01-29:
Thanks for finding this bug? 🐛 Do you mind raising a PR to fix it?

tbellembois, 2025-01-29:
Yes, I will do it.

tbellembois, 2025-01-30:
added: https://github.com/ob-f/OpenBot/pull/479

Closed 2025-01-30.

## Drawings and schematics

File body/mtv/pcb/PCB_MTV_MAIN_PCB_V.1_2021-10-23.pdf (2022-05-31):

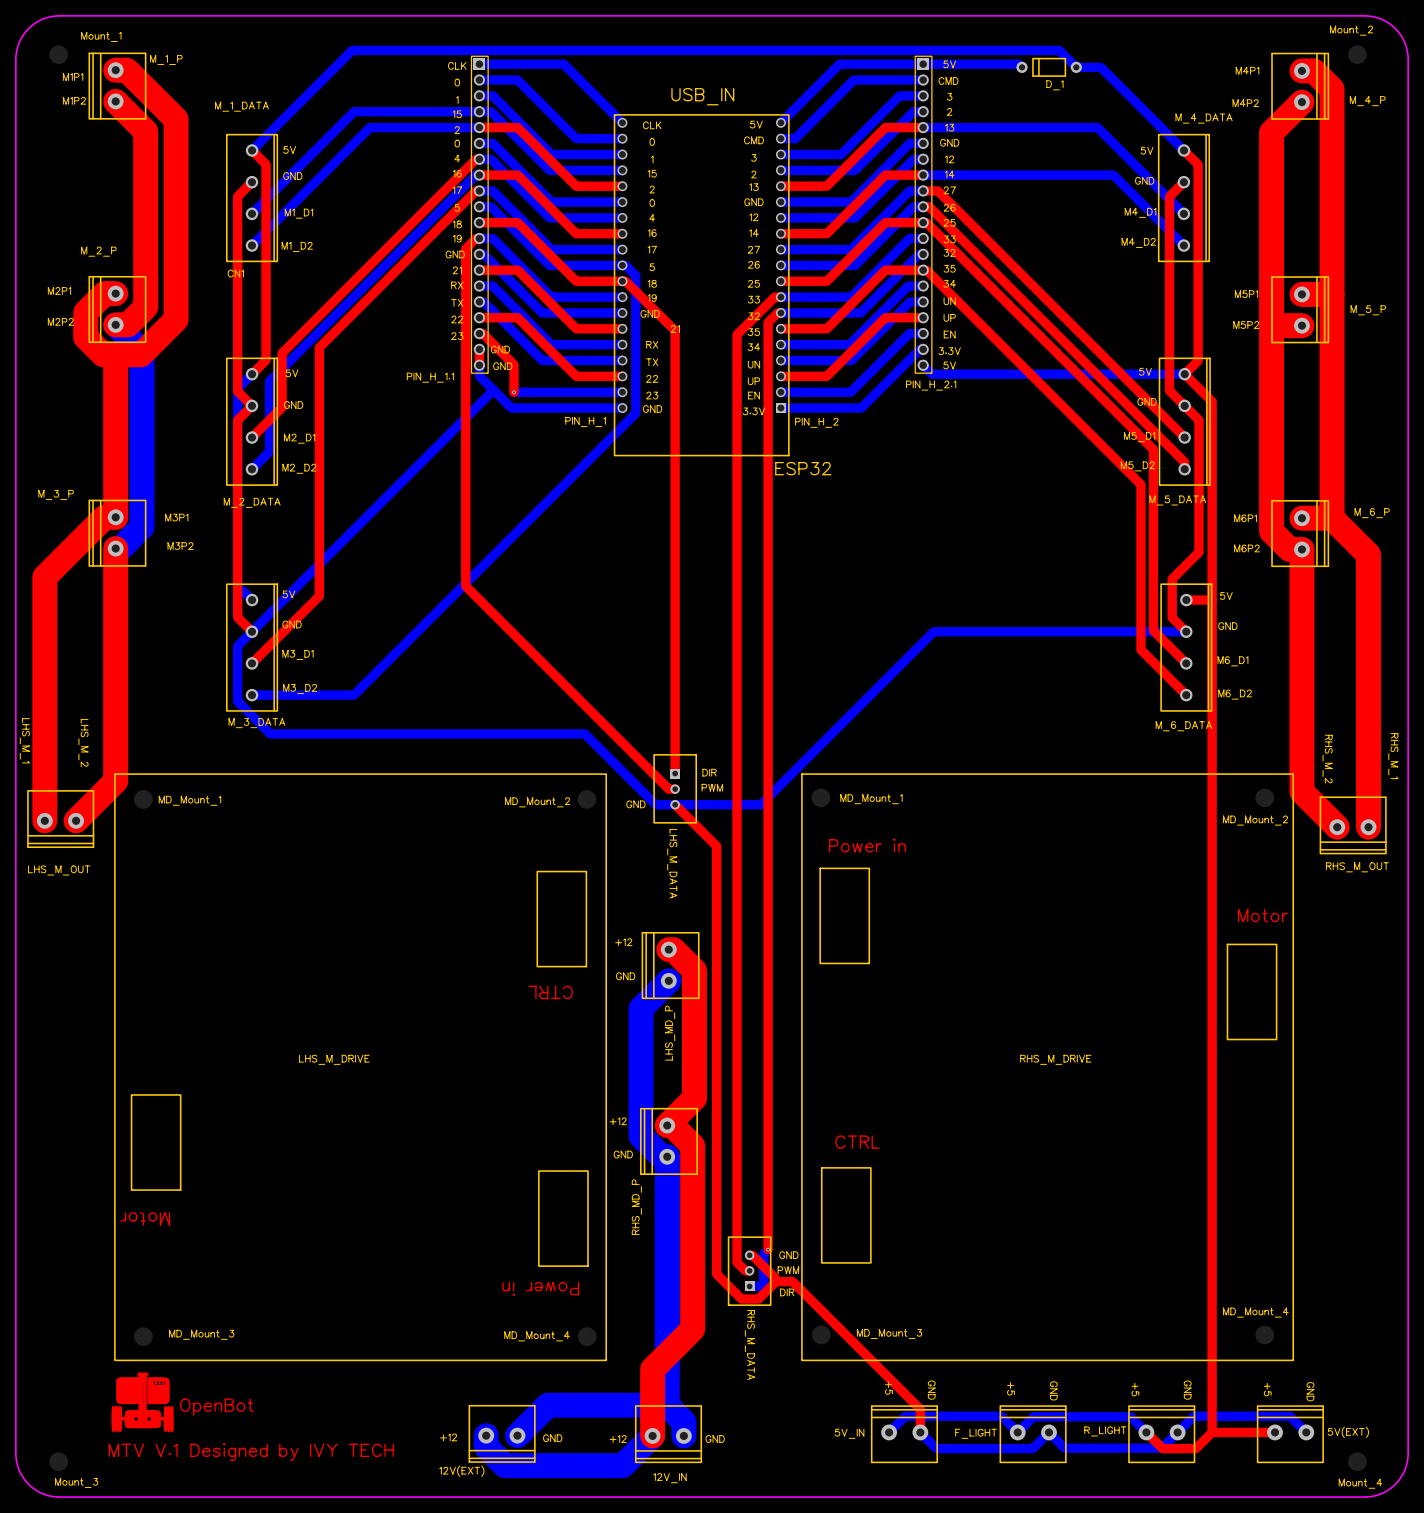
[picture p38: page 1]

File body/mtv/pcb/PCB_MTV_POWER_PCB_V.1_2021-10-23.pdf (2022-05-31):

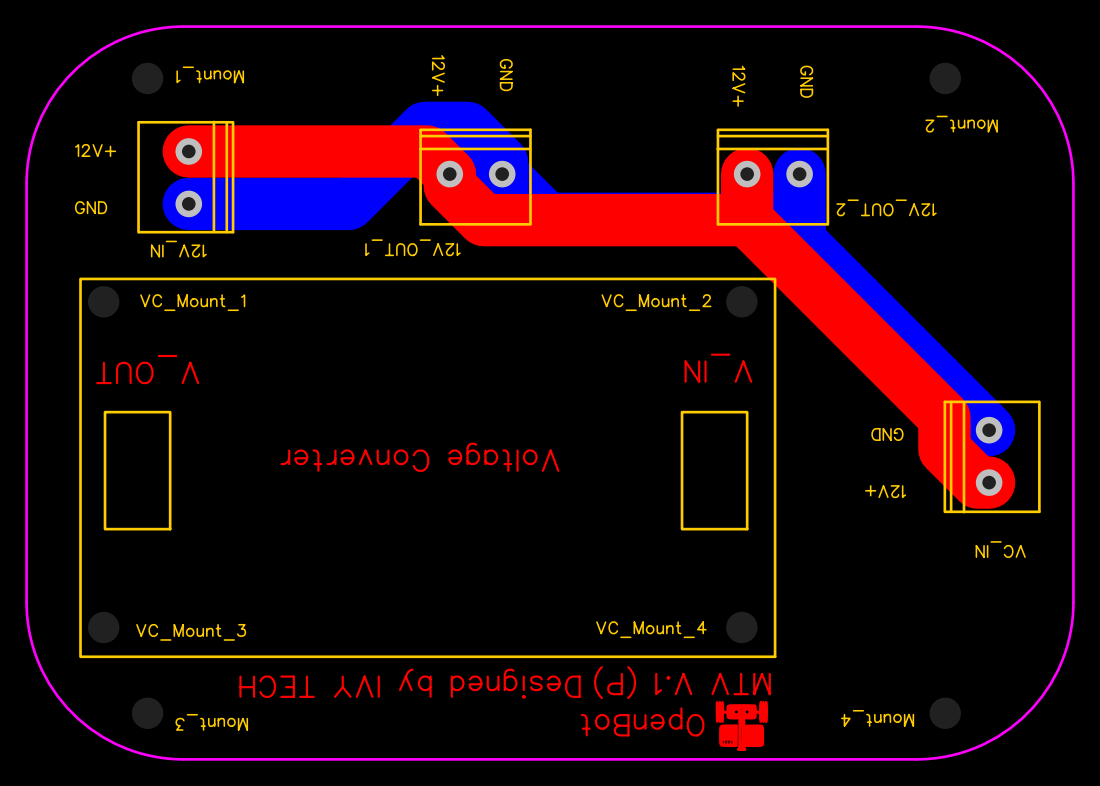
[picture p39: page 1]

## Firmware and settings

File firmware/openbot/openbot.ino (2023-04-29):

// Required App Version: 0.7.0
// ---------------------------------------------------------------------------
// This Arduino Nano sketch accompanies the OpenBot Android application.
//
// The sketch has the following functionalities:
//  - receive control commands and sensor config from Android application (USB serial)
//  - produce low-level controls (PWM) for the vehicle
//  - toggle left and right indicator signals
//  - wheel odometry based on optical speed sensors
//  - estimate battery voltage via voltage divider
//  - estimate distance based on sonar sensor
//  - control LEDs for status and at front and back of vehicle
//  - send sensor readings to Android application (USB serial)
//  - display vehicle status on OLED
//
// Dependencies: Install via "Tools --> Manage Libraries" (type library name in the search field)
//  - Interrupts: PinChangeInterrupt by Nico Hood (read speed sensors and sonar)
//  - OLED: Adafruit_SSD1306 & Adafruit_GFX (display vehicle status)
//  - Servo: Built-In library by Michael Margolis (required for RC truck)
// Contributors:
//  - October 2020: OLED display support by Ingmar Stapel
//  - December 2021: RC truck support by Usman Fiaz
//  - March 2022: OpenBot-Lite support by William Tan
//  - May 2022: MTV support by Quentin Leboutet
//  - Jan 2023: BLE support by iTinker
// ---------------------------------------------------------------------------

// By Matthias Mueller, 2023
// ---------------------------------------------------------------------------

//------------------------------------------------------//
// DEFINITIONS - DO NOT CHANGE!
//------------------------------------------------------//

//MCUs
#define NANO 328 //Atmega328p
#define ESP32 32 //ESP32

//Robot bodies with Atmega328p as MCU --> Select Arduino Nano as board
#define DIY 0        // DIY without PCB
#define PCB_V1 1     // DIY with PCB V1
#define PCB_V2 2     // DIY with PCB V2
#define RTR_TT 3     // Ready-to-Run with TT-motors
#define RC_CAR 4     // RC truck prototypes
#define LITE 5       // Smaller DIY version for education
//Robot bodies with ESP32 as MCU --> Select ESP32 Dev Module as board
#define RTR_TT2 6   // Ready-to-Run with TT-motors
#define RTR_520 7    // Ready-to-Run with 520-motors
#define MTV 8        // Multi Terrain Vehicle
#define DIY_ESP32 9  // DIY without PCB

//------------------------------------------------------//
// SETUP - Choose your body
//------------------------------------------------------//

// Setup the OpenBot version (DIY, PCB_V1, PCB_V2, RTR_TT, RC_CAR, LITE, RTR_TT2, RTR_520, DIY_ESP32)
#define OPENBOT DIY

//------------------------------------------------------//
// SETTINGS - Global settings
//------------------------------------------------------//

// Enable/Disable no phone mode (1,0)
// In no phone mode:
// - the motors will turn at 75% speed
// - the speed will be reduced if an obstacle is detected by the sonar sensor
// - the car will turn, if an obstacle is detected within TURN_DISTANCE
// WARNING: If the sonar sensor is not setup, the car will go full speed forward!
#define NO_PHONE_MODE 0

// Enable/Disable debug print (1,0)
#define DEBUG 0

// Enable/Disable coast mode (1,0)
// When no control is applied, the robot will either coast (1) or actively stop (0)
boolean coast_mode = 1;

//------------------------------------------------------//
// CONFIG - update if you have built the DIY version
//------------------------------------------------------//
// HAS_VOLTAGE_DIVIDER                  Enable/Disable voltage divider (1,0)
// VOLTAGE_DIVIDER_FACTOR               The voltage divider factor is computed as (R1+R2)/R2
// HAS_INDICATORS                       Enable/Disable indicators (1,0)
// HAS_SONAR                            Enable/Disable sonar (1,0)
// SONAR_MEDIAN                         Enable/Disable median filter for sonar measurements (1,0)
// HAS_BUMPER                           Enable/Disable bumper (1,0)
// HAS_SPEED_SENSORS_FRONT              Enable/Disable front speed sensors (1,0)
// HAS_SPEED_SENSORS_BACK               Enable/Disable back speed sensors (1,0)
// HAS_SPEED_SENSORS_MIDDLE             Enable/Disable middle speed sensors (1,0)
// HAS_OLED                             Enable/Disable OLED display (1,0)
// HAS_LEDS_FRONT                       Enable/Disable front LEDs
// HAS_LEDS_BACK                        Enable/Disable back LEDs
// HAS_LEDS_STATUS                      Enable/Disable status LEDs
// HAS_BLUETOOTH                        Enable/Disable bluetooth connectivity (1,0)
// NOTE: HAS_BLUETOOTH will only work with the ESP32 board (RTR_TT2, RTR_520, MTV, DIY_ESP32)

// PIN_TRIGGER                          Arduino pin tied to trigger pin on ultrasonic sensor.
// PIN_ECHO                             Arduino pin tied to echo pin on ultrasonic sensor.
// MAX_SONAR_DISTANCE                   Maximum distance we want to ping for (in centimeters).
// PIN_PWM_T                            Low-level control of throttle via PWM (for OpenBot RC only)
// PIN_PWM_S                            Low-level control of steering via PWM (for OpenBot RC only)
// PIN_PWM_L1,PIN_PWM_L2                Low-level control of left DC motors via PWM
// PIN_PWM_R1,PIN_PWM_R2                Low-level control of right DC motors via PWM
// PIN_VIN                              Measure battery voltage via voltage divider
// PIN_SPEED_LB, PIN_SPEED_RB           Measure left and right back wheel speed
// PIN_SPEED_LF, PIN_SPEED_RF           Measure left and right front wheel speed
// PIN_LED_LB, PIN_LED_RB               Control left and right back LEDs (indicator signals, illumination)
// PIN_LED_LF, PIN_LED_RF               Control left and right front LEDs (illumination)
// PIN_LED_Y, PIN_LED_G, PIN_LED_B      Control yellow, green and blue status LEDs

//-------------------------DIY--------------------------//
#if (OPENBOT == DIY)
const String robot_type = "DIY";
#define MCU NANO
#define HAS_VOLTAGE_DIVIDER 0
const float VOLTAGE_DIVIDER_FACTOR = (20 + 10) / 10;
const float VOLTAGE_MIN = 2.5f;
const float VOLTAGE_LOW = 9.0f;
const float VOLTAGE_MAX = 12.6f;
const float ADC_FACTOR = 5.0 / 1023;
#define HAS_INDICATORS 0
#define HAS_SONAR 0
#define SONAR_MEDIAN 0
#define HAS_SPEED_SENSORS_FRONT 0
#define HAS_OLED 0
const int PIN_PWM_L1 = 5;
const int PIN_PWM_L2 = 6;
const int PIN_PWM_R1 = 9;
const int PIN_PWM_R2 = 10;
const int PIN_SPEED_LF = 2;
const int PIN_SPEED_RF = 3;
const int PIN_VIN = A7;
const int PIN_TRIGGER = 12;
const int PIN_ECHO = 11;
const int PIN_LED_LI = 4;
const int PIN_LED_RI = 7;

//-------------------------PCB_V1-----------------------//
#elif (OPENBOT == PCB_V1)
const String robot_type = "PCB_V1";
#define MCU NANO
#define HAS_VOLTAGE_DIVIDER 1
const float VOLTAGE_DIVIDER_FACTOR = (100 + 33) / 33;
const float VOLTAGE_MIN = 2.5f;
const float VOLTAGE_LOW = 9.0f;
const float VOLTAGE_MAX = 12.6f;
const float ADC_FACTOR = 5.0 / 1023;
#define HAS_INDICATORS 1
#define HAS_SONAR 1
#define SONAR_MEDIAN 0
#define HAS_SPEED_SENSORS_FRONT 1
#define HAS_OLED 0
const int PIN_PWM_L1 = 9;
const int PIN_PWM_L2 = 10;
const int PIN_PWM_R1 = 5;
const int PIN_PWM_R2 = 6;
const int PIN_SPEED_LF = 2;
const int PIN_SPEED_RF = 4;
const int PIN_VIN = A7;
const int PIN_TRIGGER = 3;
const int PIN_ECHO = 3;
const int PIN_LED_LI = 7;
const int PIN_LED_RI = 8;

//-------------------------PCB_V2-----------------------//
#elif (OPENBOT == PCB_V2)
const String robot_type = "PCB_V2";
#define MCU NANO
#define HAS_VOLTAGE_DIVIDER 1
const float VOLTAGE_DIVIDER_FACTOR = (20 + 10) / 10;
const float VOLTAGE_MIN = 2.5f;
const float VOLTAGE_LOW = 9.0f;
const float VOLTAGE_MAX = 12.6f;
const float ADC_FACTOR = 5.0 / 1023;
#define HAS_INDICATORS 1
#define HAS_SONAR 1
#define SONAR_MEDIAN 0
#define HAS_SPEED_SENSORS_FRONT 1
#define HAS_OLED 0
const int PIN_PWM_L1 = 9;
const int PIN_PWM_L2 = 10;
const int PIN_PWM_R1 = 5;
const int PIN_PWM_R2 = 6;
const int PIN_SPEED_LF = 2;
const int PIN_SPEED_RF = 3;
const int PIN_VIN = A7;
const int PIN_TRIGGER = 4;
const int PIN_ECHO = 4;
const int PIN_LED_LI = 7;
const int PIN_LED_RI = 8;

//-------------------------RTR_TT-----------------------//
#elif (OPENBOT == RTR_TT)
const String robot_type = "RTR_TT";
#define MCU NANO
#define HAS_VOLTAGE_DIVIDER 1
const float VOLTAGE_DIVIDER_FACTOR = (30 + 10) / 10;
const float VOLTAGE_MIN = 2.5f;
const float VOLTAGE_LOW = 9.0f;
const float VOLTAGE_MAX = 12.6f;
const float ADC_FACTOR = 5.0 / 1023;
#define HAS_INDICATORS 1
#define HAS_SONAR 1
#define SONAR_MEDIAN 0
#define HAS_BUMPER 1
#define HAS_SPEED_SENSORS_FRONT 1
#define HAS_SPEED_SENSORS_BACK 1
#define HAS_LEDS_FRONT 1
#define HAS_LEDS_BACK 1
#define HAS_LEDS_STATUS 1
const int PIN_PWM_L1 = 10;
const int PIN_PWM_L2 = 9;
const int PIN_PWM_R1 = 6;
const int PIN_PWM_R2 = 5;
const int PIN_SPEED_LF = A3;
const int PIN_SPEED_RF = 7;
const int PIN_SPEED_LB = A4;
const int PIN_SPEED_RB = 8;
const int PIN_VIN = A6;
const int PIN_TRIGGER = 4;
const int PIN_ECHO = 2;
const int PIN_LED_LI = A5;
const int PIN_LED_RI = 12;
const int PIN_LED_LB = A5;
const int PIN_LED_RB = 12;
const int PIN_LED_LF = 3;
const int PIN_LED_RF = 11;
const int PIN_LED_Y = 13;
const int PIN_LED_G = A0;
const int PIN_LED_B = A1;
const int PIN_BUMPER = A2;
const int BUMPER_NOISE = 512;
const int BUMPER_EPS = 10;
const int BUMPER_AF = 951;
const int BUMPER_BF = 903;
const int BUMPER_CF = 867;
const int BUMPER_LF = 825;
const int BUMPER_RF = 786;
const int BUMPER_BB = 745;
const int BUMPER_LB = 607;
const int BUMPER_RB = 561;

//-------------------------RC_CAR-----------------------//
#elif (OPENBOT == RC_CAR)
const String robot_type = "RC_CAR";
#define MCU NANO
#include <Servo.h>
Servo ESC;
Servo SERVO;
#define HAS_VOLTAGE_DIVIDER 0
const float VOLTAGE_DIVIDER_FACTOR = (20 + 10) / 10;
const float VOLTAGE_MIN = 0.0f;
const float VOLTAGE_LOW = 6.4f;
const float VOLTAGE_MAX = 8.4f;
const float ADC_FACTOR = 5.0 / 1023;
#define HAS_INDICATORS 0
#define HAS_SONAR 0
#define SONAR_MEDIAN 0
const int PIN_PWM_T = A0;
const int PIN_PWM_S = A1;
const int PIN_VIN = A7;
const int PIN_TRIGGER = 4;
const int PIN_ECHO = 4;
const int PIN_LED_LI = 7;
const int PIN_LED_RI = 8;

//-------------------------LITE-------------------------//
#elif (OPENBOT == LITE)
const String robot_type = "LITE";
#define MCU NANO
const float VOLTAGE_MIN = 2.5f;
const float VOLTAGE_LOW = 4.5f;
const float VOLTAGE_MAX = 5.0f;
#define HAS_INDICATORS 1
const int PIN_PWM_L1 = 5;
const int PIN_PWM_L2 = 6;
const int PIN_PWM_R1 = 9;
const int PIN_PWM_R2 = 10;
const int PIN_LED_LI = 4;
const int PIN_LED_RI = 7;

//-------------------------RTR_TT2----------------------//
#elif (OPENBOT == RTR_TT2)
const String robot_type = "RTR_TT2";
#define MCU ESP32
#include <esp_wifi.h>
#define HAS_BLUETOOTH 1
#define analogWrite ledcWrite
#define attachPinChangeInterrupt attachInterrupt
#define detachPinChangeInterrupt detachInterrupt
#define digitalPinToPinChangeInterrupt digitalPinToInterrupt
#define PIN_PWM_L1 CH_PWM_L1
#define PIN_PWM_L2 CH_PWM_L2
#define PIN_PWM_R1 CH_PWM_R1
#define PIN_PWM_R2 CH_PWM_R2
#define HAS_VOLTAGE_DIVIDER 1
const float VOLTAGE_DIVIDER_FACTOR = (30 + 10) / 10;
const float VOLTAGE_MIN = 6.0f;
const float VOLTAGE_LOW = 9.0f;
const float VOLTAGE_MAX = 12.6f;
const float ADC_FACTOR = 3.3 / 4095;
#define HAS_INDICATORS 1
#define HAS_SONAR 1
#define SONAR_MEDIAN 0
#define HAS_BUMPER 1
#define HAS_SPEED_SENSORS_FRONT 1
#define HAS_SPEED_SENSORS_BACK 1
#define HAS_LEDS_FRONT 1
#define HAS_LEDS_BACK 1
#define HAS_LEDS_STATUS 1
//PWM properties
const int FREQ = 5000;
const int RES = 8;
const int CH_PWM_L1 = 0;
const int CH_PWM_L2 = 1;
const int CH_PWM_R1 = 2;
const int CH_PWM_R2 = 3;
const int CH_LED_LF = 4;
const int CH_LED_RF = 5;
const int CH_LED_LB = 6;
const int CH_LED_RB = 7;
const int PIN_PWM_LF1 = 16;
const int PIN_PWM_LF2 = 17;
const int PIN_PWM_LB1 = 19;
const int PIN_PWM_LB2 = 18;
const int PIN_PWM_RF1 = 25;
const int PIN_PWM_RF2 = 26;
const int PIN_PWM_RB1 = 32;
const int PIN_PWM_RB2 = 33;
const int PIN_SPEED_LF = 21;
const int PIN_SPEED_RF = 35;
const int PIN_SPEED_LB = 23;
const int PIN_SPEED_RB = 36;
const int PIN_VIN = 39;
const int PIN_TRIGGER = 12;
const int PIN_ECHO = 14;
const int PIN_LED_LI = 22;
const int PIN_LED_RI = 27;
const int PIN_LED_LB = 22;
const int PIN_LED_RB = 27;
const int PIN_LED_LF = 4;
const int PIN_LED_RF = 13;
const int PIN_LED_Y = 0;
const int PIN_LED_G = 2;
const int PIN_LED_B = 15;
const int PIN_BUMPER = 34;
const int BUMPER_NOISE = 512;
const int BUMPER_EPS = 50;
const int BUMPER_AF = 3890;
const int BUMPER_BF = 3550;
const int BUMPER_CF = 3330;
const int BUMPER_LF = 3100;
const int BUMPER_RF = 2930;
const int BUMPER_BB = 2750;
const int BUMPER_LB = 2180;
const int BUMPER_RB = 2000;
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
void loop() {

#if (HAS_BLUETOOTH)
  // disconnecting
  if (!deviceConnected && oldDeviceConnected) {
    delay(500);                     // give the bluetooth stack the chance to get things ready
    bleServer->startAdvertising();  // restart advertising
    Serial.println("Waiting a client connection to notify...");
    oldDeviceConnected = deviceConnected;
  }
  // connecting
  if (deviceConnected && !oldDeviceConnected) {
    oldDeviceConnected = deviceConnected;
  }
#endif

#if (NO_PHONE_MODE)
  if ((millis() - turn_direction_time) >= turn_direction_interval) {
    turn_direction_time = millis();
    turn_direction = random(2);  //Generate random number in the range [0,1]
  }
  // Drive forward
  if (distance_estimate > 3 * TURN_DISTANCE) {
    ctrl_left = distance_estimate;
    ctrl_right = ctrl_left;
    digitalWrite(PIN_LED_LI, LOW);
    digitalWrite(PIN_LED_RI, LOW);
  }
  // Turn slightly
  else if (distance_estimate > 2 * TURN_DISTANCE) {
    ctrl_left = distance_estimate;
    ctrl_right = ctrl_left / 2;
  }
  // Turn strongly
  else if (distance_estimate > TURN_DISTANCE) {
    ctrl_left = ctrl_max;
    ctrl_right = -ctrl_max;
  }
  // Drive backward slowly
  else {
    ctrl_left = -ctrl_slow;
    ctrl_right = -ctrl_slow;
    digitalWrite(PIN_LED_LI, HIGH);
    digitalWrite(PIN_LED_RI, HIGH);
  }
  // Flip controls if needed and set indicator light
  if (ctrl_left != ctrl_right) {
    if (turn_direction > 0) {
      int temp = ctrl_left;
      ctrl_left = ctrl_right;
      ctrl_right = temp;
      digitalWrite(PIN_LED_LI, HIGH);
      digitalWrite(PIN_LED_RI, LOW);
    } else {
      digitalWrite(PIN_LED_LI, LOW);
      digitalWrite(PIN_LED_RI, HIGH);
    }
  }

  // Enforce limits
  ctrl_left = ctrl_left > 0 ? max(ctrl_min, min(ctrl_left, ctrl_max)) : min(-ctrl_min, max(ctrl_left, -ctrl_max));
  ctrl_right = ctrl_right > 0 ? max(ctrl_min, min(ctrl_right, ctrl_max)) : min(-ctrl_min, max(ctrl_right, -ctrl_max));
#else  // Check for messages from the phone
  if (Serial.available() > 0) {
    on_serial_rx();
  }
  if (distance_estimate <= STOP_DISTANCE && ctrl_left > 0 && ctrl_right > 0) {
    ctrl_left = 0;
    ctrl_right = 0;
  }
  if ((millis() - heartbeat_time) >= heartbeat_interval) {
    ctrl_left = 0;
    ctrl_right = 0;
  }
#endif

#if HAS_BUMPER
  if (analogRead(PIN_BUMPER) > BUMPER_NOISE && !bumper_event) {
    delayMicroseconds(500);
    for (unsigned int i = 0; i < bumper_array_sz; i++) {
      bumper_array[i] = analogRead(PIN_BUMPER);
    }
    bumper_reading = get_median(bumper_array, bumper_array_sz);
    if (bumper_reading > BUMPER_NOISE)
      emergency_stop();
  }

  bool collison_front = collision_lf || collision_rf || collision_cf;
  bool collision_back = collision_lb || collision_rb;
  bool control_front = ctrl_left > 0 && ctrl_right > 0;
  bool control_back = ctrl_left < 0 && ctrl_right < 0;

  if (!bumper_event || (control_back && collison_front) || (control_front && collision_back)) {
    update_vehicle();
  }
#else
  update_vehicle();
#endif

#if HAS_VOLTAGE_DIVIDER
  // Measure voltage
  vin_array[vin_counter % vin_array_sz] = analogRead(PIN_VIN);
  vin_counter++;
#endif

#if HAS_SONAR
  // Check for successful sonar reading
  if (!sonar_sent && ping_success) {
    distance = echo_time * US_TO_CM;
    update_distance_estimate();
    send_sonar_reading();
    sonar_sent = true;
  }
  // Measure distance every sonar_interval
  if ((millis() - sonar_time) >= max(sonar_interval, MAX_SONAR_TIME)) {
    if (!sonar_sent && !ping_success) {  // Send max val if last ping was not returned
      distance = MAX_SONAR_DISTANCE;
      update_distance_estimate();
      send_sonar_reading();
      sonar_sent = true;
    }
    sonar_time = millis();
    sonar_sent = false;
    send_ping();
  }
#endif

#if HAS_INDICATORS
  // Check indicator signal every indicator_interval
  if ((millis() - indicator_time) >= indicator_interval) {
    update_indicator();
    indicator_time = millis();
  }
#endif

#if HAS_BUMPER
  // Check bumper signal every bumper_interval
  if ((millis() - bumper_time) >= bumper_interval && bumper_event) {
    reset_bumper();
    bumper_time = millis();
  }
#endif
#if HAS_VOLTAGE_DIVIDER
  // Send voltage reading via serial
  if ((millis() - voltage_time) >= voltage_interval) {
    send_voltage_reading();
    voltage_time = millis();
  }
#endif
#if (HAS_SPEED_SENSORS_FRONT or HAS_SPEED_SENSORS_BACK or HAS_SPEED_SENSORS_MIDDLE)
  // Send wheel odometry reading via serial
  if ((millis() - wheel_time) >= wheel_interval) {
    send_wheel_reading(millis() - wheel_time);
    wheel_time = millis();
  }
#endif
#if (HAS_OLED || DEBUG)
  // Display vehicle measurments for via serial every display_interval
  if ((millis() - display_time) >= display_interval) {
    display_vehicle_data();
    display_time = millis();
  }
#endif
}

//------------------------------------------------------//
// FUNCTIONS
//------------------------------------------------------//
#if HAS_VOLTAGE_DIVIDER

float get_voltage() {
  unsigned long array_sum = 0;
  unsigned int array_size = min(vin_array_sz, vin_counter);
  for (unsigned int index = 0; index < array_size; index++) {
    array_sum += vin_array[index];
  }
  return float(array_sum) / array_size * ADC_FACTOR * VOLTAGE_DIVIDER_FACTOR;
}

#endif

void update_vehicle() {
#if (OPENBOT == RC_CAR)
  update_throttle();
  update_steering();
#elif (OPENBOT == MTV)
  update_left_motors_mtv();
  update_right_motors_mtv();
#else
  update_left_motors();
  update_right_motors();
#endif
}

#if (OPENBOT == RC_CAR)
void update_throttle() {
  if (ctrl_left == 0 || ctrl_right == 0) {
    ESC.write(90);  //set throttle to zero
  } else {
    int throttle = map(ctrl_left + ctrl_right, -510, 510, 0, 180);
    ESC.write(throttle);
  }
}

void update_steering() {
  int steering = map(ctrl_left - ctrl_right, -510, 510, 0, 180);
  if (ctrl_left + ctrl_right < 0) {
    SERVO.write(steering);
  } else {
    SERVO.write(180 - steering);
  }
}

#elif (OPENBOT == MTV)
void update_left_motors_mtv() {
  if (ctrl_left < 0) {
    ledcWrite(LHS_PWM_OUT, -ctrl_left);
    digitalWrite(PIN_DIR_L, HIGH);
  } else if (ctrl_left > 0) {
    ledcWrite(LHS_PWM_OUT, ctrl_left);
    digitalWrite(PIN_DIR_L, LOW);
  } else {
    if (coast_mode) {
      coast_left_motors_mtv();
    } else {
      stop_left_motors_mtv();
    }
  }
}

void stop_left_motors_mtv() {
  ledcWrite(LHS_PWM_OUT, 0);
  digitalWrite(PIN_DIR_L, LOW);
}

void coast_left_motors_mtv() {
  ledcWrite(LHS_PWM_OUT, 0);
  digitalWrite(PIN_DIR_L, LOW);
}

void update_right_motors_mtv() {
  if (ctrl_right < 0) {
    ledcWrite(RHS_PWM_OUT, -ctrl_right);
    digitalWrite(PIN_DIR_R, HIGH);
  } else if (ctrl_right > 0) {
    ledcWrite(RHS_PWM_OUT, ctrl_right);
    digitalWrite(PIN_DIR_R, LOW);
  } else {
    if (coast_mode) {
      coast_right_motors_mtv();
    } else {
      stop_right_motors_mtv();
    }
  }
}

void stop_right_motors_mtv() {
  ledcWrite(RHS_PWM_OUT, 0);
  digitalWrite(PIN_DIR_R, LOW);
}

void coast_right_motors_mtv() {
  ledcWrite(RHS_PWM_OUT, 0);
  digitalWrite(PIN_DIR_R, LOW);
}

#else

void update_left_motors() {
  if (ctrl_left < 0) {
    analogWrite(PIN_PWM_L1, -ctrl_left);
    analogWrite(PIN_PWM_L2, 0);
  } else if (ctrl_left > 0) {
    analogWrite(PIN_PWM_L1, 0);
    analogWrite(PIN_PWM_L2, ctrl_left);
  } else {
    if (coast_mode) {
      coast_left_motors();
    } else {
      stop_left_motors();
    }
  }
}

void stop_left_motors() {
  analogWrite(PIN_PWM_L1, 255);
  analogWrite(PIN_PWM_L2, 255);
}

void coast_left_motors() {
  analogWrite(PIN_PWM_L1, 0);
  analogWrite(PIN_PWM_L2, 0);
}

void update_right_motors() {
  if (ctrl_right < 0) {
    analogWrite(PIN_PWM_R1, -ctrl_right);
    analogWrite(PIN_PWM_R2, 0);
  } else if (ctrl_right > 0) {
    analogWrite(PIN_PWM_R1, 0);
    analogWrite(PIN_PWM_R2, ctrl_right);
  } else {
    if (coast_mode) {
      coast_right_motors();
    } else {
      stop_right_motors();
    }
  }
}

void stop_right_motors() {
  analogWrite(PIN_PWM_R1, 255);
  analogWrite(PIN_PWM_R2, 255);
}

void coast_right_motors() {
  analogWrite(PIN_PWM_R1, 0);
  analogWrite(PIN_PWM_R2, 0);
}

#endif

boolean almost_equal(int a, int b, int eps) {
  return abs(a - b) <= eps;
}
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

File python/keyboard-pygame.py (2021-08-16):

import pygame
from pygame.locals import *
import cv2 # pip3 install opencv-python
import os
import threading
import json
from common import *
import argparse


s_socket = ServerSocket()

white = (255, 255, 255)
black = (0, 0, 0)
blue = (0, 0, 128)
red = (200, 0, 0)

class CommandHandler:

    def __init__(self):
        pygame.key.set_repeat(200)

    left = DriveValue()
    right = DriveValue()

    def send_command(self, command):
        s_socket.send('{{command: {command} }}\n'.format(command=command))

    def send_drive_command(self, left, right):
        s_socket.send('{{driveCmd: {{l:{l}, r:{r} }} }}\n'.format(l=left, r=right))

    def reset(self):
        self.send_drive_command(self.left.reset(), self.right.reset())

    def forward_left(self):
        self.send_drive_command(self.left.write(0.75), self.right.max())

    def forward_right(self):
        self.send_drive_command(self.left.max(), self.right.write(0.75))

    def backward_left(self):
        self.send_drive_command(self.left.min(), self.right.write(-0.75))

    def backward_right(self):
        self.send_drive_command(self.left.write(-0.75), self.right.min())

    def rotate_left(self):
        self.send_drive_command(self.left.min(), self.right.max())

    def rotate_right(self):
        self.send_drive_command(self.left.max(), self.right.min())

    def go_forward(self):
        self.send_drive_command(self.left.max(), self.right.max())

    def go_backward(self):
        self.send_drive_command(self.left.min(), self.right.min())

    def handle_keys(self):
        while True:
            for event in pygame.event.get():
                if event.type == pygame.QUIT:
                    running = False

                if event.type == pygame.KEYUP:
                    if event.key==K_w:
                        self.reset()

                    elif event.key in [K_a, K_d, K_q, K_e]:
                        if(pygame.key.get_pressed()[pygame.K_w]):
                            self.go_forward()
                        elif(pygame.key.get_pressed()[pygame.K_s]):
                            self.go_backward()    
                        else:
                            self.reset()

                    elif event.key==K_s:
                        self.reset()

                if event.type == pygame.KEYDOWN:
                    if event.key==K_w:
                        self.go_forward()

                    elif event.key==K_s:
                        self.go_backward()

                    elif event.key==K_a:
                        if(pygame.key.get_pressed()[pygame.K_w]):
                            self.forward_left()
                        elif(pygame.key.get_pressed()[pygame.K_s]):
                            self.backward_left()

                    elif event.key==K_d:
                        if(pygame.key.get_pressed()[pygame.K_w]):
                            self.forward_right()
                        elif(pygame.key.get_pressed()[pygame.K_s]):
                            self.backward_right()

                    elif event.key==K_q:
                        self.rotate_left()

                    elif event.key==K_e:
                        self.rotate_right()

                    if event.key==pygame.K_n: self.send_command("NOISE")
                    if event.key==pygame.K_SPACE: self.send_command("LOGS")
                    if event.key==pygame.K_RIGHT: self.send_command("INDICATOR_RIGHT")
                    if event.key==pygame.K_LEFT: self.send_command("INDICATOR_LEFT")
                    if event.key==pygame.K_UP: self.send_command("INDICATOR_STOP")
                    if event.key==pygame.K_DOWN: self.send_command("NETWORK")
                    if event.key==pygame.K_m: self.send_command("DRIVE_MODE")
                    if event.key==pygame.K_ESCAPE:
                        return

(zc, info) = register("OPEN_BOT_CONTROLLER", 19400)

class VideoPlayer:
    def set_stream (self, stream):
        self.stream = stream

    def play_video(self):
        if not self.stream:
            print(f'Stream not set')
            return

        print(f'Opening the stream...')
        cap = cv2.VideoCapture(self.stream)

        # read one frame and check if there was no problem
        print(f'Checking the stream...')
        ret, img = cap.read()
        if not ret:
            print("Can't read stream")
            cap.release()
            cv2.destroyAllWindows()
            return

        img = cv2.cvtColor(img, cv2.COLOR_BGR2RGB)
        img = cv2.transpose(img)

        # display its width, height, color_depth
        print('Stream resolution:', img.shape)
        shape = img.shape
        width = img.shape[0]
        height = img.shape[1]
    
        display_flags = DOUBLEBUF | HWSURFACE # | SCALED
        if pygame.display.mode_ok(size=(width, height), flags=display_flags ):
            video_screen = pygame.display.set_mode(size=(width, height), flags=display_flags)
        else:
            raise ValueError("error initializing display, can not get mode")

        print (f'Display: {pygame.display.Info()}')

        running = True
        while running:

            # read one frame and check if there was no problem
            ret, img = cap.read()
            if not ret:
                running = False
                cap.release()
                cv2.destroyAllWindows()
                break

            else:
                img = cv2.cvtColor(img, cv2.COLOR_BGR2RGB)
                img = cv2.transpose(img)

                # blit directly on screen         
                pygame.surfarray.blit_array(video_screen, img)

            pygame.display.flip()

    def stop_video(self):
        print(f'Stopping video...')
        pass

def usage():
    usageStr = """
    Make sure to keep the pygame window in focus!\r
    
    Use the following keys to drive the robot:\r

    \tW:        Go forward\r
    \tS:        Go backward\r
    \tA:        Turn slightly left (while driving)\r
    \tD:        Turn slightly right (while driving)\r
    \tQ:        Rotate left\r
    \tE:        Rotate right\r

    \tM:        Drive mode\r
    \tN:        Toggle noise\r
    \tLeft:     Left indicator\r
    \tRight:    Right indicator\r
    \tUp:       Cancel indicators\r
    \tDown:     Network mode\r
    \tSPACE:    Toggle logging\r
    \tESC:      Quit\r
    """

    return usageStr

def run_receiver ():
    while True:
        try:
            data = s_socket.receive()
            print(f'Received: {data}\r')

            if data in ["", None]:
                return

            handle_status(data)

        except Exception as e:
            print(f'run_receiver: Got exception: {e}\r')
            break

video_player = VideoPlayer()
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

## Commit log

2020-08-24 Update robot body README
    [body_bottom.stl, body_top.stl, phone_mount_bottom.stl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]
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2020-08-27 Fix STL link
2020-08-27 Add slim version of body_bottom
    [body_bottom_slim.stl]
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2020-08-28 Update README.md
    The Amazon links for the tires and Motor Driver were unavailable. Updated with link that has them in stock.
2020-08-29 Add source source files and slim version
    [body_bottom.step, body_top.step, body_top_slim.stl]
2020-08-31 Add PCB instructions
    [BOM.csv, centroid_file.csv]
2020-09-01 Add Chinese Readme file (#12)
    * Add the Chinese lang readme file, update 2 links.
    * Translate custom PCB instruction to Chinese.
    * Translate Android build instruction to Chinese.
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2020-09-10 Add step files for phone mount
    [phone_mount_bottom.step, phone_mount_top.step]
2020-09-16 Update PCB and READMEs
    [BOM_v1.csv, BOM_v2.csv, centroid_file_v1.csv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]
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2020-09-20 Add Glueable Body for printers with small volumes
    [bottom_glue.step, bottom_glue.stl, openbot_bottom_A.step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]
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2020-09-21 Adjust slim body, organize files (#52)
    - Adjust slim body to fit on 220x220mm build plate
    - Organize CAD models into folders
    - Organize PCB files into folders
    [BOM_v1.csv, BOM_v2.csv, body_bottom.step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]
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2020-09-23 Add the standard minimum build plate dimensions
    Adds a line describing what the minimal build plate dimensions should be for the standard (not slim) body.
2020-09-24 Update info about REAME_CN
    switch size fixed, usb cable link fixed, price recommendations for 3d print
2020-09-26 Update firmware and documentation (#60)
    * Refactor and improve the instructions
    * Update firmware and instructions, support PCB_V1 and PCB_V2
    * Refactor: markdown lint
    * Fix some links
2020-10-07 Update firmware (#77)
    * Stop by sonar
    * No phone mode
    * Refactoring
    * Update documentation
2020-10-13 Update readme (#83)
    * Update README
    * Update pins for DIY build
    * Update wiring diagram
2020-11-12 Update README.md
    - Add description for alternatives to 3D printing
    - Add OLED links
2020-11-15 major firmware update (#112)
    * several improvements to make code more readable and compact
    * removed NewPing due to many reported issues (e.g. interference on pin 8, pin 3 and 11 not usable as PWM, etc.)
    * implemented interrupt based ultrasonic sensor readings
    * implemented interrupt based speed sensor readings for all hardware configurations
    * all main features/sensors can enabled/disabled with flags so the firmware only contains the functionalities needed and is as fast and extensible as possible
    * improved NO_PHONE_MODE
2020-11-15 thias15/readme tuning (#113)
    * instructions for getting the code
    * add/update some images
    * compress stl files
    [glue_body_top_B.stl, glue_connector_bottom.stl, glue_connector_top_A.stl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]
2020-11-16 Android bugfix (#114)
    * update gradle and SDK versions
    * fix control in person following for negative sensor rotation
2020-11-19 Button to switch camera (#115)
    * Add camera toggle button and add some logic
    * Dynamic camera toggle button text assignment
    * Persistent camera through orientation changes
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2020-12-06 Handle buttons from controller. Do not handle motion events yet. Now keeps the connection open even if we are re-selecting SmartphoneController.
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2020-12-30 integrate camera base using view binding
2020-12-30 refactor view binding camera methods
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2021-01-05 add phone controller docs (#140)
    - Added README.md file and technical overview PDF document for the controller app and how it connects to the OpenBot app.
    - Added support for Android 5.1 device (SDK 21) for the controller app.
    - Moved screen management from the main ControllerActivity into a ScreenManager class.
2021-01-06 Move noise and sensorReading into public classes
2021-01-12 change speed mode via game controller, fix back button issue
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2021-01-20 fix stl files
    [glue_body_bottom_A.stl, glue_body_bottom_B.stl, glue_body_top_A.stl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]
2021-01-22 enable kotlin support, add usb attached intent filter to main activity, apply style file
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2021-01-22 remove device attached intent from network activity to avoid duplicate alert
2021-01-22 sonar color fix
2021-01-23 fix buggy UI interaction on controller button click
2021-01-25 Issue #152
    🧑🏻‍🔧 👨🏻‍🔧 👩🏻‍🔬 🧑🏻‍🔬 👨🏻‍🔬 👩🏻‍🎨
2021-01-27 Update Vehicle.java
    fix battery limits
2021-01-29 move vehicle disconnection out to main activity and add usb status button to free roam game mode
2021-02-09 swap game controller buttons to toggle speed mode for consistency
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2021-02-10 swap speed mode buttons on game controller for consistency
2021-02-17 gpu to cpu thread count fix
2021-02-18 camera toggle change on rotate fix. double detection text due to debig fix
2021-02-18 fragment attached crash check
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2021-03-03 1. set usb button always enabled in free roam 2. initialise vehicle class only if it is not null
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2021-03-16 Ivo/video streaming 2 (#162)
    * Reversed Server/Client for Controller/Bot. The controller is now server, because in needs input from the user when new connection is established.
    * Added wifi direct
    * Updated technical documentation for controller app.
    * WIP, video streaming
    * Added another way to connect using LAN and Network Services. This keeps the IP address stable, so we can stream video.
    * Improve video ion RTSP server.
    * Improve reliability of RTSP stream
    * In order to stabilize connections, we now no longer connect and disconnect when the controller is selected/deselected. Instead, when another device is selected, we will just stop sending/receiving at application level.
    * All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
2021-03-18 fix thread closure on screent timeout
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2021-04-10 Ivo/keyboard controller (#173)
    * Added a python example on how to connect and communicate to the smartphone app from a Raspberry Pi.
    * Added python script `keyboard-controller.py` to control the robot remotely.
    * Updated README file.
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2021-04-17 bugfix: remove person class filter
2021-04-26 Ivo/keyboard controller UI (#182)
    - Added Python keyboard controller with video from robot. More work is to be done on this to display some keys, usage, speed, etc. (experimental)
    - Video has smaller latency, higher resolution and full screen. Also added sound. (experimental)
    - Network connection type is selected based on availability of WiFi. Now the controller can operate outside using NearBy connection if no WiFi is present (experimental)
    - The drive controls are reverted back to home position if touch is released.
    - RTSP video stream stopped/started when controller is disconnected/connected. This was a bug in the previous version.
    [common.py]
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2021-04-29 specify interface to prevent WinError 10049
    [common.py]
2021-04-30 Ivo/RTSP server fixes (#185)
    - Delay starting the RTSP client 1 second to improve staring issues.
    - Move setting resolution from RtspServer to PhoneController
    - Select Nearby connection when WiFi is turned off.
    [keyboard-pygame.py]
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2021-05-04 1. copy add model only after user approves it 2. focus edit model name on edit button click
2021-05-06 fix number of threads displayed
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2021-06-21 Ivo/webrtc (#192)
    * Added Video/Audio streaming via WebRTC.
    * The surface in the bot app to send video to the controller is created programmatically and is independent of the fragment.
    * Controller creates its video view type (RTSP or WebRTC) dynamically based on settings in the bot app.
    * Added a message to the keyboard-pygame.py to warn that WebRTC video is not supported yet.
    * Added video mirror and audio mute/unmute.
    * Bugfixes.
    [keyboard-pygame.py]
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2021-07-21 Added accelerator and a break pedal to 'drive-by-tilt' screen. Removed kill switch in the main app
2021-07-22 App crashes in Autopilot fragment, when Autopilot switch is activated (#210)
    * Update controllInfo textView from the main thread
2021-07-22 Fix app crash in object tracking fragment (Android 6) (#212)
    * Updating controllInfo textView from the main thread
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2021-07-26 - Decelerate after releasing accelerator pedal - Brake pedal can put the robot in reverse - Updated the README file.
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2021-12-20 Fix initial mirroing if image. Stop WrbRTC in Esc. Fix error after exiting full screen. Reset robot on shutdown.
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2021-12-30 OpenBot RC-Truck v1.0 (#241)
    * Create README file for rc_truck_body
    * Add CAD files for RC truck
    * Update CAD files for phone mount
    [camera_elevator.step, camera_elevator.stl, electronics_cover.step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]
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2022-01-30 voltage limits + fixes
2022-01-30 sonar fix + formatting
    [openbot_nano.ino]
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2022-03-06 Revert to DIY as default
    [openbot_nano.ino]
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2022-03-09 reverse coasting convention for LITE
    [openbot_nano.ino]
2022-03-14 lite readme + refactor
    [BOM_v1.csv, BOM_v2.csv, body_bottom.step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]
2022-03-31 A short firmware fix for the coast_mode issue.
    [openbot_nano.ino]
2022-05-31 Multi-Terrain Vehicle (MTV) (#278)
    * added MTV content
    * removed duplicate copy of the phone mount
    * reduce image file size
    * integrated MTV firmware
    [100deg_Joint.step, 100deg_Joint.stl, 100deg_Joint_Mirror.step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]
2022-05-31 Ready-to-Run OpenBot (#285)
    * add readme
    * add cad files
    * add images
    * add pcb files
    [BOM_BaseBoard_Arduino_V1A.csv, BOM_BaseBoard_Arduino_V1B.csv, BOM_BaseBoard_Arduino_V1C.csv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]
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2022-11-25 fix: flip image for front camera
2022-11-30 Adjust robot speed by a estimated distancefactor calculated from track box area in relation to screen area, assuming that the tracking box is lage if close to tracked object/person and apply the fact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
2022-12-17 improve resume, checkpointing, plotting
    - save last, best train, best val checkpoints instead of keeping so many
    - keep track of initial epoch when resuming to fix logging
    - unify batch visualization
2022-12-17 Deprecate redundant code (CameraActivity.getScreenOrientation, redundant with ImageUtils.getScreenOrientation) for (later) deletion. The later is already more often used.
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2023-01-11 Added download of test_data and test_model
    - implemented get_data function in test_download_data.py that downloads
    test_data and test_model if not already available
    - all test files that require test_data and test_model call get_data
    first
    - small fix in realsense.py: if no realsense present, then the thread
    won't start. Otherwise, the thread would crash
    - updated readme
    [download_data.py, realsense.py]
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2023-04-05 add cad models
    [block_body_top.step, block_body_top.stl, block_body_top_big.step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]
2023-04-05 bottom parts
    [block_body_bottom.step, block_body_bottom.stl]
2023-04-05 fix typo
    [block_body_bottom.step]
2023-04-07 Adding BLE support on Android Device + DPAD controller Connection (#330)
    * adding all the changes for bluetooth for ble connection, sending data to ble device and managing devices.
    * commenting extra toasts
    * adding null checks
    * upgrade android api
    * upgrade android sdk version of controller and gradle lint build failed issue solved
    * update python style
    * Bump express from 4.17.1 to 4.18.2 in /policy/frontend
    Bumps [express](https://github.com/expressjs/express) from 4.17.1 to 4.18.2.
    - [Release notes](https://github.com/expressjs/express/releases)
    - [Changelog](https://github.com/expressjs/express/blob/master/History.md)
    - [Commits](https://github.com/expressjs/exp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
    [openbot.ino]
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2023-05-24 Corrected couple of other minor visual issues and updated doc image.
2023-05-24 Node.js Web controller client UI improvements (#359)
    - styled controls and buttons
    - added top bar
    - improved video layout and responsiveness
    - changed font
    - fixed styling and updated screenshot in README.md
    - made keys have fixed sizing and a subtle shadow
    - added symbols to arrow keys
2023-12-28 Mirror the target control of ObjectNavFragment if front facing camera is used (#386)
    - Mirror the target control of ObjectNavFragment if front facing camera is used
    - The convention for the front camera varies across phones. Adding an icon to mirror controls next to the camera flip icon, instead of always mirroring control when using front camera.
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2024-06-20 Android-blockly-updates (#394)
    1. **UI Fixes and Enhancements**:
    - Fixed bugs in webview (alert box, white theme, Google sign-in, profile picture editing).
    - Improved navigation bar in Bluetooth table and edit profile.
    - Added animations and fixed UI bugs in projects, scanner, and model management fragments.
    - Applied app-wide styling and updated the README.md.
    - Updated various screen elements (playground, bottom sheet, main screen, point goal navigation).
    - Added text-to-speech and other Blockly functions.
    - Improved sensor reading display and vehicle control synchronization.
    2. **Feature Additions**:
    - Added new functionalities: stop car button,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
2024-06-24 React Blockly (#344)
    ### Bug Fixes and Error Handling
    - Fixed crashes, syntax errors, and parameter issues.
    - Handled errors in adjacent AI blocks, AI blocks in forever blocks, and workspace.
    - Resolved bugs in point goal navigation, AI block configuration, and object tracking.
    ### Feature Additions and Enhancements
    - Added functionality for:
    - Multiple AI detection
    - Autopilot with detection pipeline
    - Dynamic frame-based detection
    - Text-to-speech
    - Detection control blocks
    - Local data saving
    - Enhanced playground, Blockly functions, and vehicle control synchronization.
    - Implemented reset functionality, user usage analytics, and subscription restrictions.
    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
2024-07-04 POC for integrating Remote web server with Openbot (#369)
    ### Summary of Changes
    #### Code Improvements
    - **Bug Fixes**:
    - Fixed syntax errors in JS generator
    - Resolved frame parameter issues
    - Updated object type handling
    - Addressed navigation issues in Blockly
    - Managed token expiration handling
    - **New Features**:
    - Added dynamic speed UI for object tracking
    - Enabled local data saving for controllers and sensor statuses
    - Integrated autopilot parameters
    - Implemented camera switch status
    - Introduced web server control and text-to-speech functionalities
    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
2024-10-07 fixed landscape orientation in object tracking and updated sign-in fingerprints (#449)
    * fixed landscape orientation in object tracking
